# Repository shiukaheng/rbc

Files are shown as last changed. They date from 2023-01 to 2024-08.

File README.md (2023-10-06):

# 🤖 RoboCapture
A photogrammetry robot designed from scratch to autonomously scan indoor spaces.

## 🛠 Development

- **Cross-Platform**: This repository is designed to be cross-platform, working on Windows, MacOS, and Linux. We leverage Docker and the devcontainer extension in VSCode to achieve this.
  
- **Testing**: Most of the development and testing have been done on Linux. However, it might require slight adjustments when setting up on other operating systems.

### 🔧 Pre-requisites

1. `$(hostname).local` should be broadcasted on the network using mDNS. This applies to both the robot and the development computer.
2. Docker must be running on a Linux environment.

### 🍎 MacOS Specifics

If you're on a Mac, you might need to adjust the Docker permissions:
```bash
sudo chown -R $(whoami) ~/.docker
```
This ensures Docker can run without requiring sudo every time.

### 🖥️ X11 Authentication

For enabling X11 forwarding, execute the following command on the host computer:
```bash
xhost +local:docker
```

### 📝 Notes
Please double-check the file permissions before making a commit to ensure they are appropriate, due to docker created files being owned by `root`. Fix shall be issued soon.

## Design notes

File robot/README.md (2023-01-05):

# 🦚 Robocock

Project Robocock is a versatile fully automated high-resolution interior photogrammetry solution.

The system will utilise [SLAM](https://www.notion.so/About-caf9711042f84a92b1a0a05f0bd871f7), an [omni wheel system](https://en.wikipedia.org/wiki/Omni_wheel), and a custom path planning algorithm to provide a moving platform to mount cameras on, of which will be connected to the onboard computer to automatically acquire images for [photogrammetry](https://www.notion.so/About-caf9711042f84a92b1a0a05f0bd871f7) while traversing the interior space.

For the field of 3D capture, this tool will be a valuable replacement to [mainstream ground-based LIDAR scanning](https://en.wikipedia.org/wiki/Lidar#Surveying), which captures geometry well, but not so much on model texture detail important for model visualization; or drone photogrammetry, since it may be impractical to fly drones in interior spaces. 

Moreover, in the recent rise in [neural radiance field research](https://www.matthewtancik.com/nerf), the dense image datasets our automation captures may also be increasingly useful.

## Roadmap
- [x]  Assemble frame
- [ ]  Install motors and wheels
- [ ]  Assemble electronics to drive wheels
- [ ]  Add sensors to frame
- [ ]  Path planning
- [ ]  Photogrammetry integration

## Setting ups

1) create directory: ~/dev_ws/src
2) clone this repository under the directory as mentioned
3) cd to dev_ws
4) build by entering: colcon build --symlink-install

## Other useful commands

1) setup bash with: source install/setup.bash
2) launch ROS with: ros2 launch robocock rsp.launch.py
3) run rviz with: ros2 run rviz2 rviz2
4) run empty joint state publisher with: ros2 run joint_state_publisher_gui joint_state_publisher_gui
5) to run gazebo with robot, launch with: ros2 launch robocock launch_sim.launch.py

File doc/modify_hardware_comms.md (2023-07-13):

- Change the motor_state.h under controller code if necessary.
- Change rbc messages
- Change hardware_parameter_server
- Change RobotHW (If impacted setpoint)

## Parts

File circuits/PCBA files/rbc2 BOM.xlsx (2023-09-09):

Comment | Designator | Footprint | JLCPCB Part #
1uF | C1 | Capacitor_SMD:C_0603_1608Metric | C696843
270uF | C2, C11, C12, C24 | EEHZS1H221P | C79124
4.7uF | C3 | Capacitor_SMD:C_1206_3216Metric | C412300
10nF | C4 | Capacitor_SMD:C_0402_1005Metric | C482489
100nF | C5, C6, C13, C14, C19, C20, C21, C22, C23, C25, C30, C31, C33 | Capacitor_SMD:C_0402_1005Metric | C2649519
10pF | C7 | Capacitor_SMD:C_0603_1608Metric | C2171298
10nF | C8, C15, C16, C26 | Capacitor_SMD:C_0805_2012Metric | C27071
22uF | C9 | Capacitor_SMD:C_1206_3216Metric | C304004
100uF | C10, C17, C18, C27 | 16SVF180M | C136275
220nF | C28, C29, C32 | Capacitor_SMD:C_0805_2012Metric | C913663
450mV 3A Schottky Diode | D1, D2, D3, D5 | Diode_SMD:D_SMA | C17101
Yellow LED | D4 | Diode_SMD:D_0805_2012Metric | C84261
Green LED | D6, D7, D8, D9 | Diode_SMD:D_0805_2012Metric | C63855
Red LED | D10 | Diode_SMD:D_0805_2012Metric | C86865
LT8609AEDDM#PBF | IC1 | SON50P300X300X80-11N-D | C673976
LM2678SX-ADJ/NOPB | IC2, IC3, IC4, IC5 | KTW0007B | C40844
BTN70301EPAXUMA1 | IC6, IC7, IC8, IC9, IC10, IC11 | Infineon_PG-TSDSO-14-22 | C3655686
DNP | J1 | TerminalBlock_Phoenix:TerminalBlock_Phoenix_MKDS-3-2-5.08_1x02_P5.08mm_Horizontal
DNP | J2 | Connector_PinHeader_2.54mm:PinHeader_2x02_P2.54mm_Vertical
DNP | J3 | Connector_PinHeader_2.54mm:PinHeader_2x02_P2.54mm_Vertical
DNP | J4 | Connector_PinHeader_2.54mm:PinHeader_2x02_P2.54mm_Vertical
DNP | J5 | TerminalBlock_Phoenix:TerminalBlock_Phoenix_MKDS-3-2-5.08_1x02_P5.08mm_Horizontal
DNP | J6 | Connector_Molex:Molex_Micro-Fit_3.0_43045-0612_2x03_P3.00mm_Vertical
DNP | J7, J8 | Connector_Molex:Molex_Micro-Fit_3.0_43045-0412_2x02_P3.00mm_Vertical
DNP | J9, J10, J11 | Connector_Molex:Molex_Micro-Fit_3.0_43045-0612_2x03_P3.00mm_Vertical
2.2uH | L1 | INDC4441X200N | C719179
22uH | L2, L3, L4, L6 | INDPM110100X400N | C2047201
10uH | L5 | Inductor_SMD:L_0805_2012Metric | C88172
18.2k | R1 | Resistor_SMD:R_0603_1608Metric_Pad0.98x0.95mm_HandSolder | C844532
1k | R2, R7, R8, R18 | Resistor_SMD:R_0201_0603Metric | C138165
187k | R3 | Resistor_SMD:R_0603_1608Metric | C227629
8.87k | R4, R9, R10, R20 | Resistor_SMD:R_0603_1608Metric | C862310
1M | R5, R12 | Resistor_SMD:R_0402_1005Metric | C144787
100k | R6 | Resistor_SMD:R_0201_0603Metric | C100127
10k | R11, R19 | Resistor_SMD:R_0402_1005Metric | C144807
1.6k | R13 | Resistor_SMD:R_0805_2012Metric_Pad1.20x1.40mm_HandSolder | C316776
3.3k | R14 | Resistor_SMD:R_1206_3216Metric_Pad1.30x1.75mm_HandSolder | C104771
300 | R15, R21, R22, R23, R24, R25 | Resistor_SMD:R_0603_1608Metric_Pad0.98x0.95mm_HandSolder | C203500
82k ±1% | R16 | Resistor_SMD:R_0603_1608Metric_Pad0.98x0.95mm_HandSolder | C103831
18k ±5% | R17 | Resistor_SMD:R_0603_1608Metric_Pad0.98x0.95mm_HandSolder | C445839
4.7k | R26, R27, R28, R29, R32, R33, R34, R35, R36, R37, R38, R39, R40, R41, R42, R43, R44, R45, R47, R48, R49, R50, R51, R52 | Resistor_SMD:R_1206_3216Metric | C432834
1.2k | R30, R31, R46 | Resistor_SMD:R_1206_3216Metric | C340507
RESET Switch | S1 | FSM4JSMATR | C86487
CSTCE16M0V53-R0 | U1 | CSTCE16M0V53R0 | C32180
ATmega2560-16A | U2 | Package_QFP:TQFP-100_14x14mm_P0.5mm | C22460

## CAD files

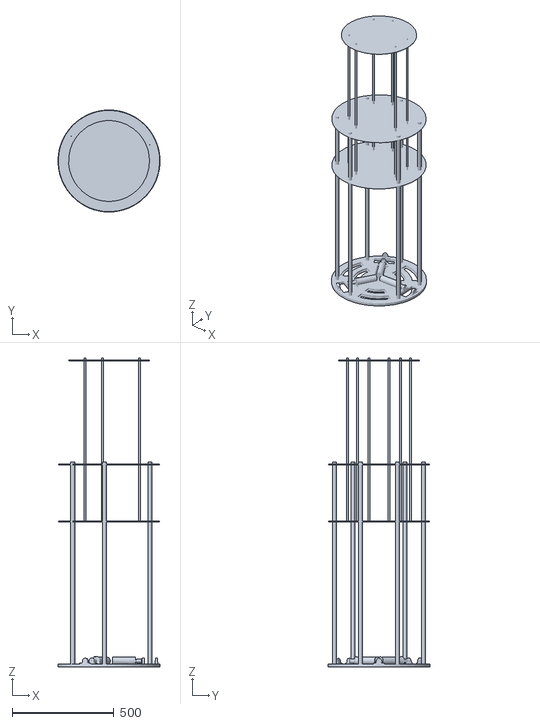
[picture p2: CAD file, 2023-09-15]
ros/rbc_base/meshes/frame_ultra_low_poly.stl
500.2 x 500.0 x 1515.0

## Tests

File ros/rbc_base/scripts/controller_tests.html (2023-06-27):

# Closed-loop testing¶

In [ ]:

%matplotlib inline
from robodev import *

In [ ]:

d = Robodev()
d.set_global_velocity(0)

[INFO] [1687739845.622243]: Waiting for base_state to start publishing...
[INFO] [1687739845.644485]: Got first message from base_state, ready!

In [ ]:

# Prerequisites
track = d.create_track().add_saw_wave(max_vel=5.0, duration=15.0, periods=3)

def apply_settings(mode: int, p_in: float, i_in: float, d_in: float, bias: float, initial_i: float = 0, plot_exclude_wheels: list = [2]):
    d.set_global_velocity(0)
    d.set_global_adaptive_state(initial_i)
    d.set_global_control_params(p_in, i_in, d_in, bias, mode)
    result = track.run()
    d.set_global_velocity(0)
    d.set_global_adaptive_state(0)
    result.plot(plot_exclude_wheels)
    result.plot_setpoint_v_velocity(plot_exclude_wheels)
    result.plot_all(plot_exclude_wheels)
    return result

# Simple PI controller¶

In [ ]:

pi = apply_settings(
    mode=1,
    p_in=40,
    i_in=10,
    d_in=0,
    bias=0
)

# PI controller with flipping biases and integrals¶

In [ ]:

pif = apply_settings(
    mode=2,
    p_in=40,
    i_in=10,
    d_in=0,
    bias=50
)

# Adaptive PID controller¶

In [ ]:

pid = apply_settings(
    mode=3,
    p_in=40,
    i_in=15.,
    d_in=0,
    bias=50
)

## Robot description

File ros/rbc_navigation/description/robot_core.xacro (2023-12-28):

<?xml version="1.0"?>
<robot xmlns:xacro="http://www.ros.org/wiki/xacro">

    <xacro:include filename="inertial_macros.xacro"/>

    <!-- links and joints go here -->

    <!-- The rest of the robot can be described from base_link, which is the centre point of the four driving wheels -->
    <link name="base_link">
    </link>

    <!-- chassis joint goes here. It connects chassis to base_link via fixed joint -->
    <joint name="chassis_joint" type="fixed">
        <parent link="base_link"/>
        <child link="chassis"/>
        <origin xyz="0 0 0"/>
    </joint> launch-prefix="bash -c 'sleep 5; $0 $@'"
    <!-- chassis description goes here. It describes the chassis of the bot which is a 54cm x 54cm x 150cm box -->
    <link name="chassis">
        <visual>
            <!-- by default, the origin is centred around the link origin, so offset it by half the height -->
            <!-- <origin xyz="0 0 0.75" rpy="0 0 0"/> -->
            <geometry>
                <!-- <box size="0.54 0.54 1.5"/> -->
                <mesh filename="package://rbc_base/meshes/frame_ultra_low_poly.stl" scale="0.001 0.001 0.001"/>
                <!-- <mesh filename="model://frame_ultra_low_poly.stl"/> -->
            </geometry>
            <material name="white"/>
        </visual>
        <!-- physics model -->
        <collision>
            <origin xyz="0 0 0.77" rpy="0 0 0"/>
            <geometry>
                <cylinder length="1.54" radius="0.25"/>
            </geometry>
        </collision>
        <xacro:inertial_cylinder mass="20" length="1.54" radius="0.25">
            <origin xyz="0 0 0.77" rpy="0 0 0"/>
        </xacro:inertial_cylinder>
    </link>
    <joint name="laser_joint" type="fixed">
        <parent link="chassis"/>
        <child link="laser"/>
        <origin xyz="0 0 0.07" rpy="0 0 0"/>
    </joint>
    <link name="laser">
        <visual>
            <origin xyz="0 0 0" rpy="0 0 0"/>
            <geometry>
                <cylinder length="0.05" radius="0.05"/>
            </geometry>
            <material name="black"/>
        </visual>
    </link>
    <!-- gazebo specific description -->
    <gazebo reference="chassis">
        <material>Gazebo/White</material>
    </gazebo>

    <!-- WHEEL 1 (CLOCKWISE) -->
    <joint name="wheel_1_joint" type="continuous">
        <parent link="base_link"/>
        <child link="wheel_1"/>
        <origin xyz="0.2 0 0" rpy="0 -${pi/2} 0"/>
        <axis xyz="0 0 1"/>
    </joint>

    <link name="wheel_1">
        <visual>
            <geometry>      
                <cylinder length="0.038" radius="0.05" />
            </geometry>
            <material name="black"/>
        </visual>
        <collision>
            <geometry>      
                <cylinder length="0.038" radius="0.05" />
            </geometry>
        </collision>
        <xacro:inertial_cylinder mass="0.2" length="0.038" radius="0.05">
            <origin xyz="0 0 0" rpy="0 0 0"/>
        </xacro:inertial_cylinder>
    </link>

    <gazebo reference="wheel_1">
        <material>Gazebo/Black</material>
        <mu1 value="0.2"/>
        <mu2 value="1.5"/>
        <kp value="10000000.0" />
        <kd value="10000.0" />
        <fdir1 value="0 0 1"/>
        <maxContacts value= "1"/>
    </gazebo>

    <!-- WHEEL 2 -->
    <joint name="wheel_2_joint" type="continuous">
        <parent link="base_link"/>
        <child link="wheel_2"/>
        <origin xyz="-0.1 -0.1732050808 0" rpy="0 ${pi/2} ${pi/3}"/>
        <axis xyz="0 0 1"/>
    </joint>

    <link name="wheel_2">
        <visual>
            <geometry>      
                <cylinder length="0.038" radius="0.05" />
            </geometry>
            <material name="black"/>
        </visual>
        <collision>
            <geometry>      
                <cylinder length="0.038" radius="0.05" />
            </geometry>
        </collision>
        <xacro:inertial_cylinder mass="0.2" length="0.038" radius="0.05">
            <origin xyz="0 0 0" rpy="0 0 0"/>
        </xacro:inertial_cylinder>
    </link>

    <gazebo reference="wheel_2">
        <material>Gazebo/Black</material>
        <mu1 value="0.2"/>
        <mu2 value="1.5"/>
        <kp value="10000000.0" />
        <kd value="10000.0" />
        <fdir1 value="0 0 1"/>
        <maxContacts value= "1"/>
    </gazebo>

    <!-- WHEEL 3 -->
    <joint name="wheel_3_joint" type="continuous">
        <parent link="base_link"/>
        <child link="wheel_3"/>
        <origin xyz="-0.1 0.1732050808 0" rpy="0 ${pi/2} -${pi/3}"/>
        <axis xyz="0 0 1"/>
    </joint>

    <link name="wheel_3">
        <visual>
            <geometry>      
                <cylinder length="0.038" radius="0.05" />
            </geometry>
            <material name="black"/>
        </visual>
        <collision>
            <geometry>      
                <cylinder length="0.038" radius="0.05" />
            </geometry>
        </collision>
        <xacro:inertial_cylinder mass="0.2" length="0.038" radius="0.05">
            <origin xyz="0 0 0" rpy="0 0 0"/>
        </xacro:inertial_cylinder>
    </link>

    <gazebo reference="wheel_3">
        <material>Gazebo/Black</material>
        <mu1 value="0.2"/>
        <mu2 value="1.5"/>
        <kp value="10000000.0" />
        <kd value="10000.0" />
        <fdir1 value="0 0 1"/>
        <maxContacts value= "1"/>
    </gazebo>

    <!-- Transmissions -->
    <transmission name="tran1">
        <type>transmission_interface/SimpleTransmission</type>
        <joint name="wheel_1_joint">
            <hardwareInterface>hardware_interface/VelocityJointInterface</hardwareInterface>
        </joint>
        <actuator name="motor_1">
            <hardwareInterface>VelocityJointInterface</hardwareInterface>
            <mechanicalReduction>1</mechanicalReduction>
        </actuator>
    </transmission>

    <transmission name="tran2">
        <type>transmission_interface/SimpleTransmission</type>
        <joint name="wheel_2_joint">
            <hardwareInterface>hardware_interface/VelocityJointInterface</hardwareInterface>
        </joint>
        <actuator name="motor_2">
            <hardwareInterface>VelocityJointInterface</hardwareInterface>
            <mechanicalReduction>1</mechanicalReduction>
        </actuator>
    </transmission>

    <transmission name="tran3">
        <type>transmission_interface/SimpleTransmission</type>
        <joint name="wheel_3_joint">
            <hardwareInterface>hardware_interface/VelocityJointInterface</hardwareInterface>
        </joint>
        <actuator name="motor_3">
            <hardwareInterface>VelocityJointInterface</hardwareInterface>
            <mechanicalReduction>1</mechanicalReduction>
        </actuator>
    </transmission>

    <gazebo>
        <plugin name="gazebo_ros_control" filename="libgazebo_ros_control.so">
        </plugin>
    </gazebo>

</robot>

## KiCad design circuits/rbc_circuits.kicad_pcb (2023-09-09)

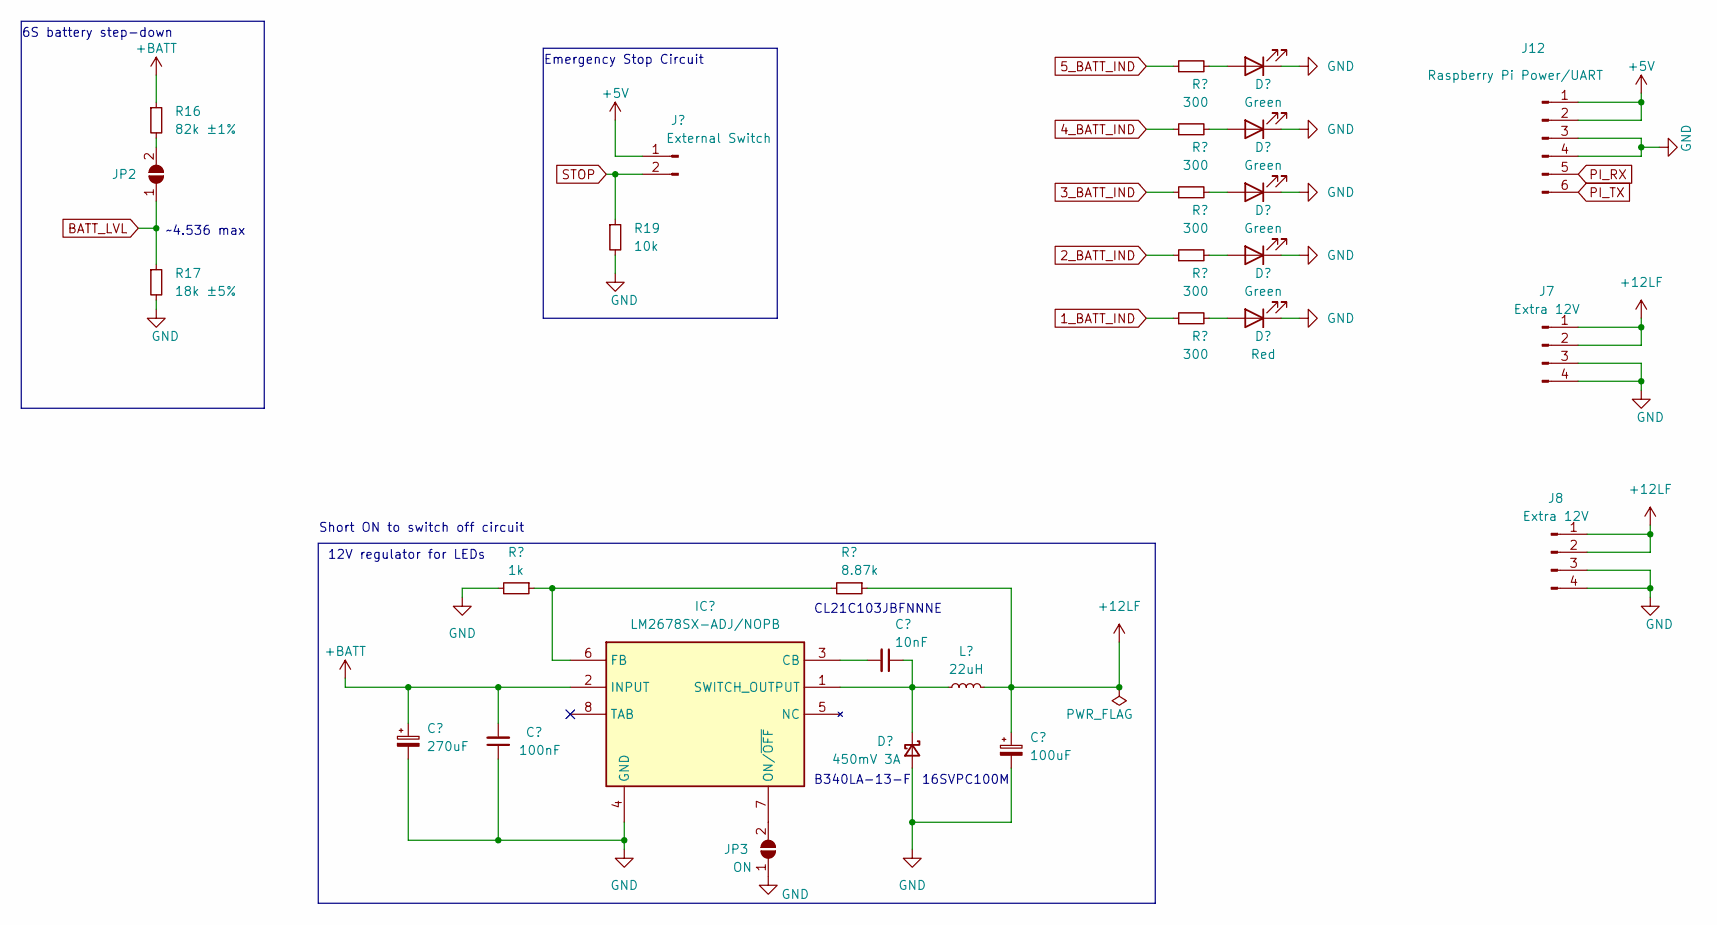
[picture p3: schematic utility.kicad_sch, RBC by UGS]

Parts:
C24: 270uF; EEHZS1H221P
C25: 100nF; C_0402_1005Metric
C26: 10nF; C_0805_2012Metric
C27: 100uF; 16SVF180M
D5: 450mV 3A; D_SMA
D6: Green; D_0805_2012Metric; Part No. 17-21/GHC-XS1T2M/3T
D7, D8, D9: Green; D_0805_2012Metric
D10: Red; D_0805_2012Metric; Part No. 17-215/R6C-AQ1R2B/3T
IC5: LM2678SX-ADJ/NOPB; KTW0007B_custom; Mouser Part Number 926-LM2678SX50NOPB
J5: External Switch; TerminalBlock_Phoenix_MKDS-3-2-5.08_1x02_P5.08mm_Horizontal
J7, J8: Extra 12V; Molex_Micro-Fit_3.0_43045-0412_2x02_P3.00mm_Vertical
J12: Raspberry Pi Power/UART; Molex_Micro-Fit_3.0_43045-0612_2x03_P3.00mm_Vertical
JP2: SolderJumper_2_Open; SolderJumper-2_P1.3mm_Open_RoundedPad1.0x1.5mm
JP3: ON; SolderJumper-2_P1.3mm_Open_RoundedPad1.0x1.5mm
L6: 22uH; INDPM110100X400N
R16: 82k ±1%; R_0603_1608Metric_Pad0.98x0.95mm_HandSolder; Part No. RTT038202FTP
R17: 18k ±5%; R_0603_1608Metric_Pad0.98x0.95mm_HandSolder
R18: 1k; R_0201_0603Metric
R19: 10k; R_0402_1005Metric
R20: 8.87k; R_0603_1608Metric
R21, R22, R23, R24, R25: 300; R_0603_1608Metric_Pad0.98x0.95mm_HandSolder

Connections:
1_BATT_IND: R25.1; also elsewhere on the board
2_BATT_IND: R24.1; also elsewhere on the board
3_BATT_IND: R23.1; also elsewhere on the board
4_BATT_IND: R22.1; also elsewhere on the board
5_BATT_IND: R21.1; also elsewhere on the board
+5V: J5.1; also elsewhere on the board
+12LF: C27.1, J7.1, J7.2, J8.1, J8.2, L6.2, R20.1
+BATT: C24.1, C25.2, IC5.2 (INPUT), R16.1; also elsewhere on the board
BATT_LVL: JP2.1 (A), R17.1; also elsewhere on the board
GND: C24.2, C25.1, C27.2, D5.2 (A), D6.1 (K), D7.1 (K), D8.1 (K), D9.1 (K), D10.1 (K), IC5.4 (GND), J7.3, J7.4, J8.3, J8.4, JP3.1 (A), R17.2, R18.2, R19.2; also elsewhere on the board
unnamed: C26.1, D5.1 (K), IC5.1 (SWITCH_OUTPUT), L6.1
unnamed: D6.2 (A), R21.2
unnamed: D7.2 (A), R22.2
unnamed: D8.2 (A), R23.2
unnamed: D9.2 (A), R24.2
unnamed: D10.2 (A), R25.2
unnamed: C26.2, IC5.3 (CB)
unnamed: IC5.6 (FB), R18.1, R20.2
unnamed: IC5.7 (ON/~OFF), JP3.2 (B)
unnamed: JP2.2 (B), R16.2
STOP: J5.2, R19.1; also elsewhere on the board

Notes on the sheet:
~4.536 max
6S battery step-down
16SVPC100M
12V regulator for LEDs
Short ON to switch off circuit
Emergency Stop Circuit
CL21C103JBFNNNE
B340LA-13-F

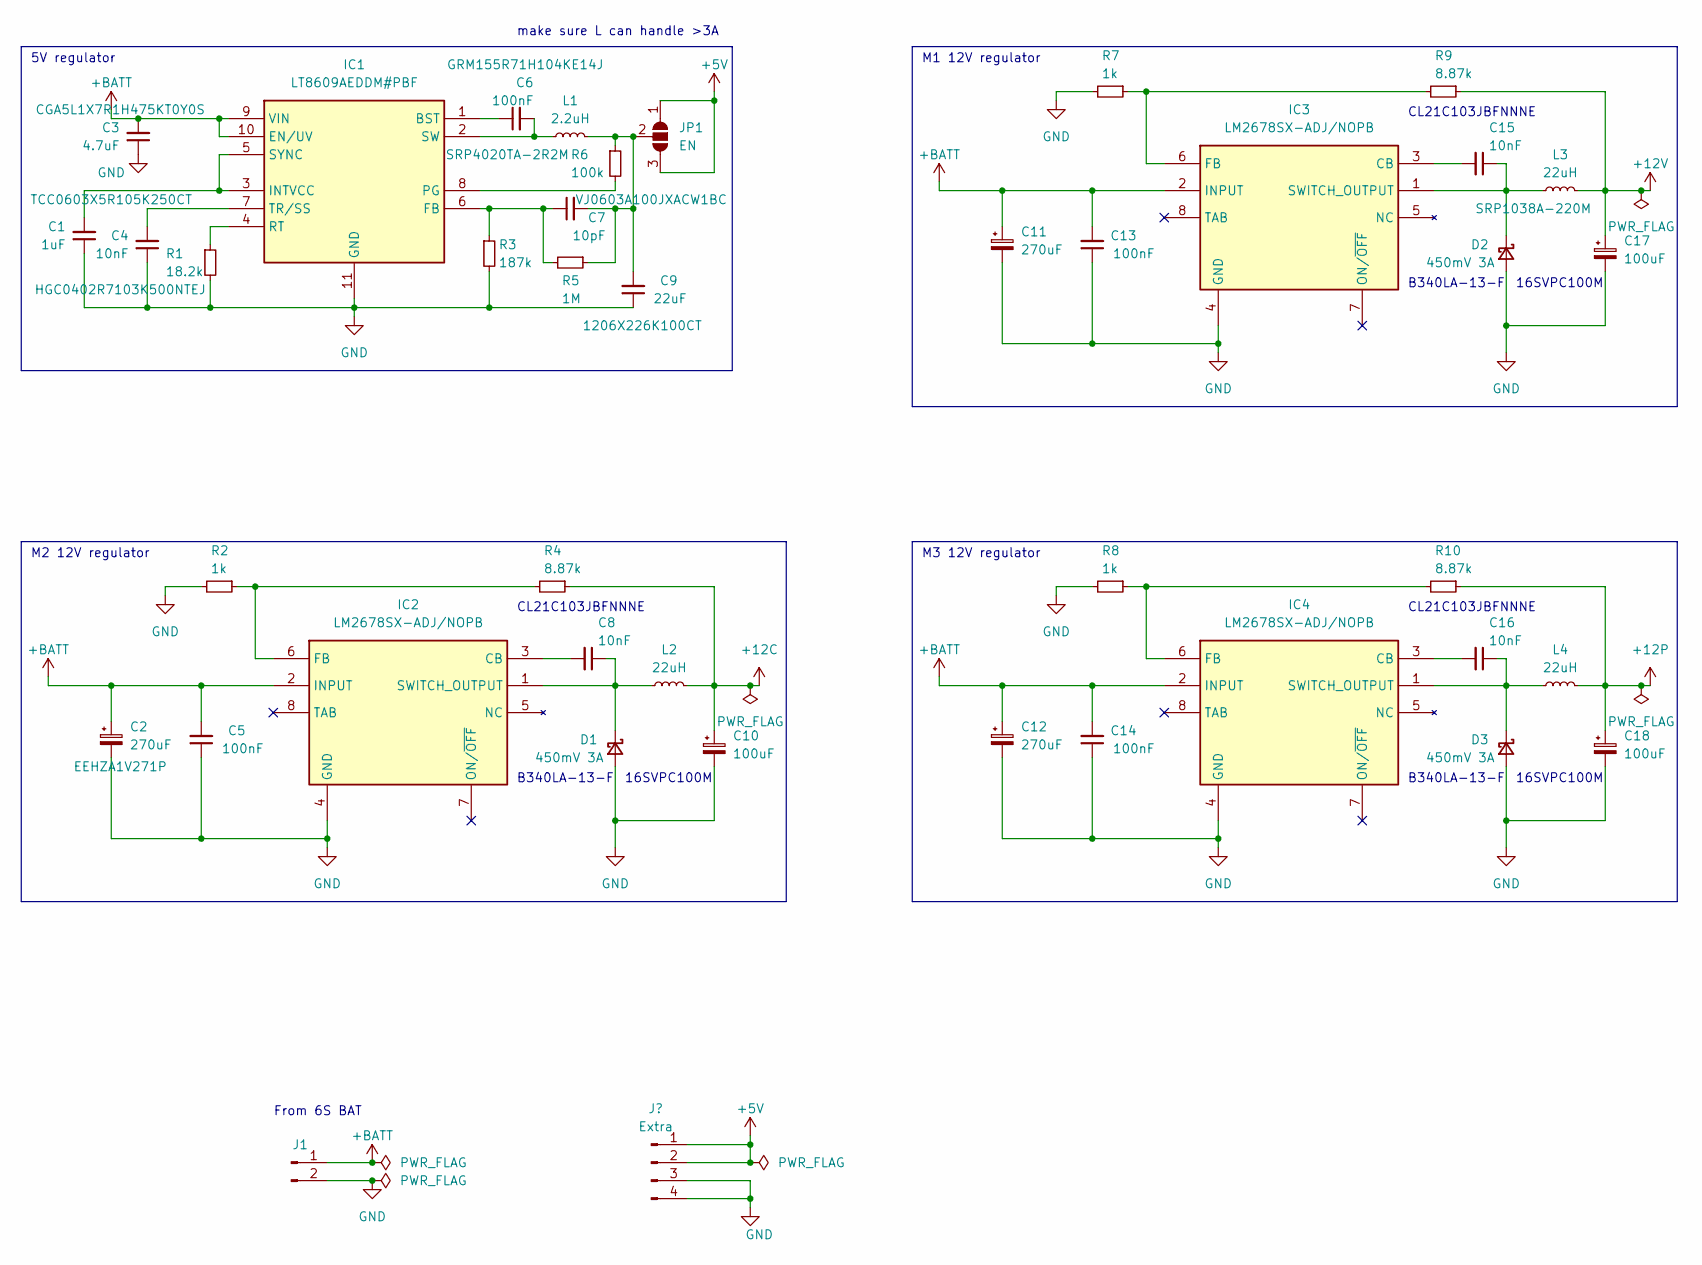
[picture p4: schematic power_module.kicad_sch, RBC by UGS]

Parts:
C1: 1uF; C_0603_1608Metric; Part No. TCC0603X5R105K250CT
C2: 270uF; EEHZS1H221P; Part No. EEHZA1V271P
C3: 4.7uF; C_1206_3216Metric; Part No. CGA5L1X7R1H475KT0Y0S
C4: 10nF; C_0402_1005Metric; Part No. HGC0402R7103K500NTEJ
C5, C13, C14: 100nF; C_0402_1005Metric
C6: 100nF; C_0402_1005Metric; Part No. GRM155R71H104KE14J
C7: 10pF; C_0603_1608Metric; Part No. VJ0603A100JXACW1BC
C8, C15, C16: 10nF; C_0805_2012Metric
C9: 22uF; C_1206_3216Metric; Part No. 1206X226K100CT
C10, C17, C18: 100uF; 16SVF180M
C11, C12: 270uF; EEHZS1H221P
D1, D2, D3: 450mV 3A; D_SMA
IC1: LT8609AEDDM#PBF; SON50P300X300X80-11N-D; Mouser Part Number 584-LT8609AEDDM#PBF
IC2, IC3, IC4: LM2678SX-ADJ/NOPB; KTW0007B_custom; Mouser Part Number 926-LM2678SX50NOPB
J1: Conn_01x02_Pin; TerminalBlock_Phoenix_MKDS-3-2-5.08_1x02_P5.08mm_Horizontal
J2: Extra; PinHeader_2x02_P2.54mm_Vertical
JP1: EN; SolderJumper-3_P2.0mm_Open_TrianglePad1.0x1.5mm
L1: 2.2uH; INDC4441X200N; Part No. SRP4020TA-2R2M
L2, L4: 22uH; INDPM110100X400N
L3: 22uH; INDPM110100X400N; Part No. SRP1038A-220M
R1: 18.2k; R_0603_1608Metric_Pad0.98x0.95mm_HandSolder; Part No. CRCW060318K2FKEA
R2: 1k; R_0201_0603Metric; Part No. RC0201FR-071KL
R3: 187k; R_0603_1608Metric; Part No. AC0603FR-07187KL
R4: 8.87k; R_0603_1608Metric; Part No. RT0603BRE078K87L
R5: 1M; R_0402_1005Metric; Part No. AC0402FR-071ML
R6: 100k; R_0201_0603Metric
R7, R8: 1k; R_0201_0603Metric
R9, R10: 8.87k; R_0603_1608Metric

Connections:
+5V: J2.1, J2.2, JP1.1 (A), JP1.3 (B); also elsewhere on the board
+12C: C10.1, L2.2, R4.1; also elsewhere on the board
+12P: C18.1, L4.2, R10.1; also elsewhere on the board
+12V: C17.1, L3.2, R9.1; also elsewhere on the board
+BATT: C2.1, C3.2, C5.2, C11.1, C12.1, C13.2, C14.2, IC1.9 (VIN), IC1.10 (EN/UV), IC2.2 (INPUT), IC3.2 (INPUT), IC4.2 (INPUT), J1.1; also elsewhere on the board
GND: C1.1, C2.2, C3.1, C4.1, C5.1, C9.1, C10.2, C11.2, C12.2, C13.1, C14.1, C17.2, C18.2, D1.2 (A), D2.2 (A), D3.2 (A), IC1.11 (GND), IC2.4 (GND), IC3.4 (GND), IC4.4 (GND), J1.2, J2.3, J2.4, R1.2, R2.2, R3.2, R7.2, R8.2; also elsewhere on the board
unnamed: C8.1, D1.1 (K), IC2.1 (SWITCH_OUTPUT), L2.1
unnamed: C15.1, D2.1 (K), IC3.1 (SWITCH_OUTPUT), L3.1
unnamed: C16.1, D3.1 (K), IC4.1 (SWITCH_OUTPUT), L4.1
unnamed: C6.1, IC1.1 (BST)
unnamed: C7.1, IC1.6 (FB), R3.1, R5.2
unnamed: C1.2, IC1.3 (INTVCC), IC1.5 (SYNC)
unnamed: IC1.8 (PG), R6.2
unnamed: IC1.4 (RT), R1.1
unnamed: C6.2, IC1.2 (SW), L1.1
unnamed: C4.2, IC1.7 (TR/SS)
unnamed: C8.2, IC2.3 (CB)
unnamed: IC2.6 (FB), R2.1, R4.2
unnamed: C15.2, IC3.3 (CB)
unnamed: IC3.6 (FB), R7.1, R9.2
unnamed: C16.2, IC4.3 (CB)
unnamed: IC4.6 (FB), R8.1, R10.2
unnamed: C7.2, C9.2, JP1.2 (C), L1.2, R5.1, R6.1

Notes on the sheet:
CL21C103JBFNNNE
16SVPC100M
B340LA-13-F
make sure L can handle >3A
From 6S BAT
M2 12V regulator
5V regulator
M3 12V regulator
M1 12V regulator

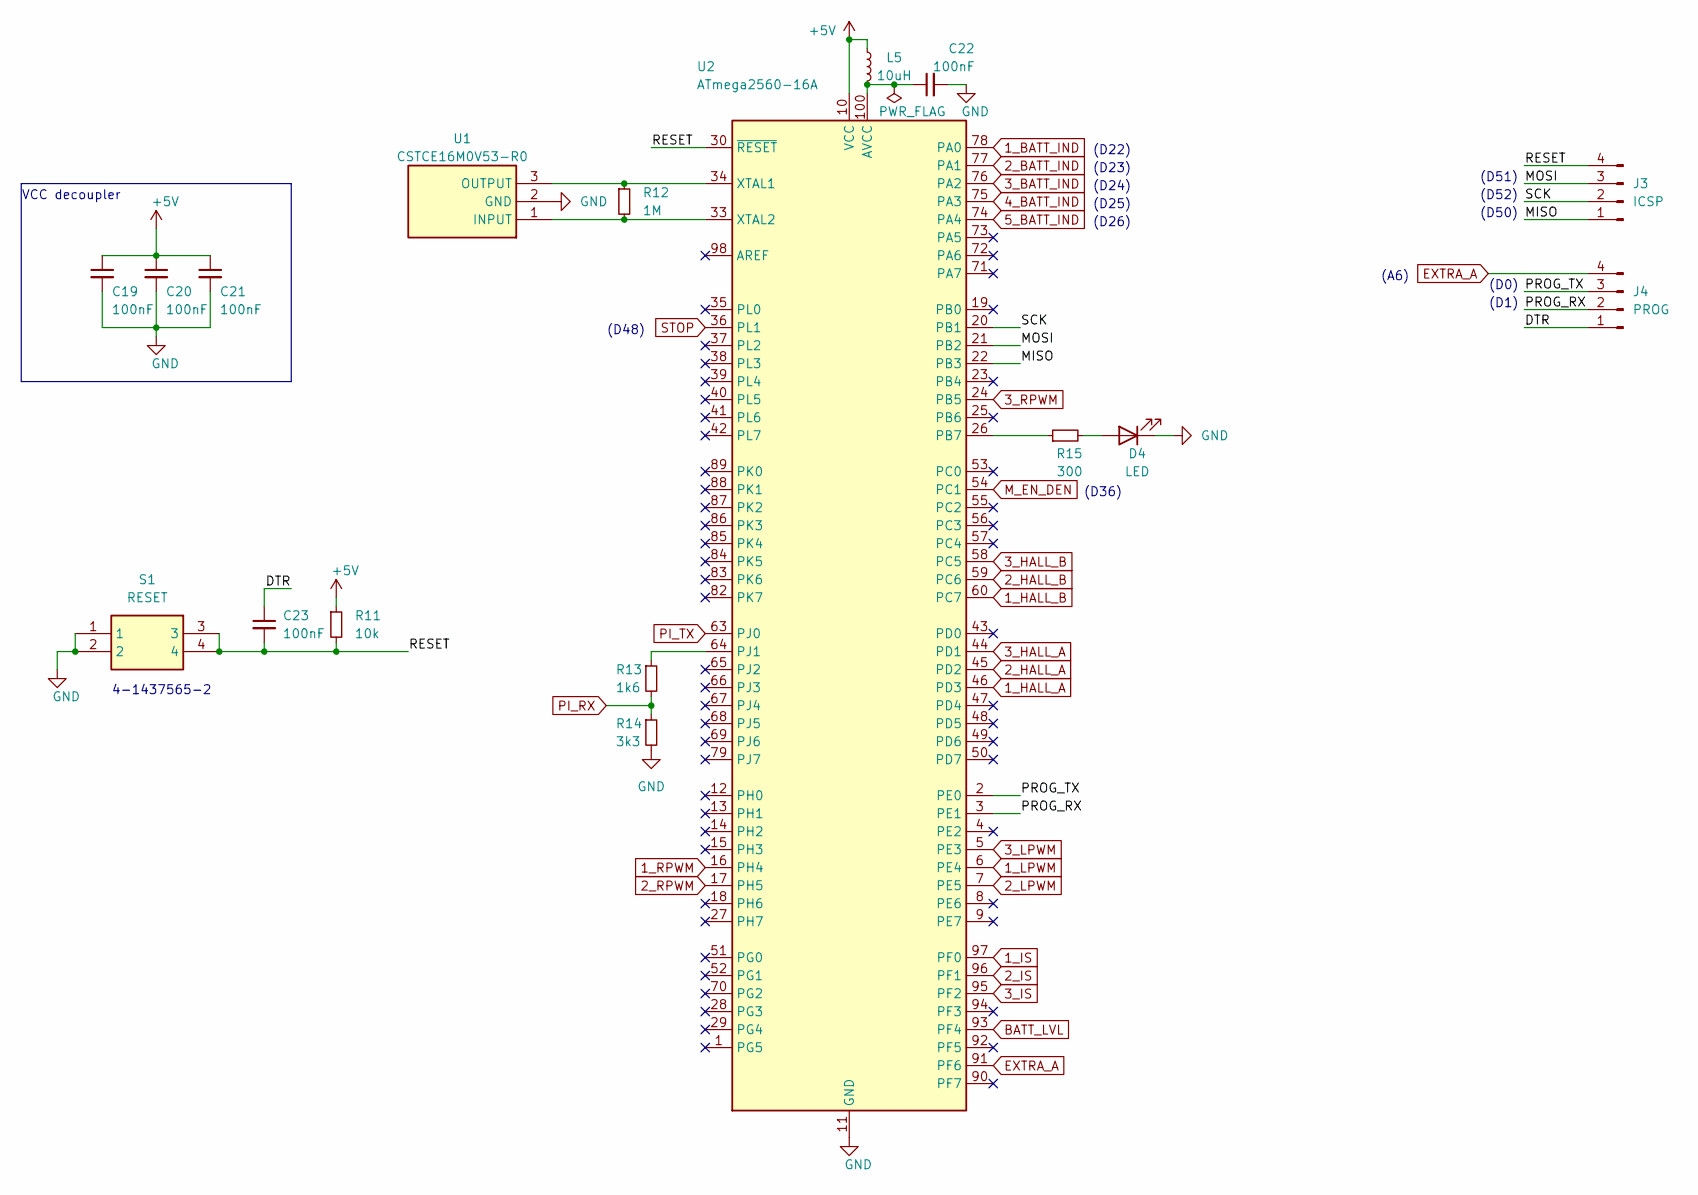
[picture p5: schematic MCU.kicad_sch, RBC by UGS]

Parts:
C19, C20, C21, C22, C23: 100nF; C_0402_1005Metric
D4: LED; D_0805_2012Metric; Part No. NCD0805Y1
J3: ICSP; PinHeader_2x02_P2.54mm_Vertical
J4: PROG; PinHeader_2x02_P2.54mm_Vertical
L5: 10uH; L_0805_2012Metric; Part No. MLZ2012M100HT000
R11: 10k; R_0402_1005Metric; Part No. AC0402FR-0710KL
R12: 1M; R_0402_1005Metric
R13: 1k6; R_0805_2012Metric_Pad1.20x1.40mm_HandSolder
R14: 3k3; R_1206_3216Metric_Pad1.30x1.75mm_HandSolder
R15: 300; R_0603_1608Metric_Pad0.98x0.95mm_HandSolder; Part No. CR0603-FX-3000ELF
S1: RESET; FSM4JSMATR; Mouser Part Number 506-FSM4JSMATR
U1: CSTCE16M0V53-R0; CSTCE16M0V53R0; Mouser Part Number 81-CSTNE16M0V530000R
U2: ATmega2560-16A; TQFP-100_14x14mm_P0.5mm

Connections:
1_BATT_IND: U2.78 (PA0); also elsewhere on the board
1_HALL_A: U2.46 (PD3); also elsewhere on the board
1_HALL_B: U2.60 (PC7); also elsewhere on the board
1_IS: U2.97 (PF0); also elsewhere on the board
1_LPWM: U2.6 (PE4); also elsewhere on the board
1_RPWM: U2.16 (PH4); also elsewhere on the board
2_BATT_IND: U2.77 (PA1); also elsewhere on the board
2_HALL_A: U2.45 (PD2); also elsewhere on the board
2_HALL_B: U2.59 (PC6); also elsewhere on the board
2_IS: U2.96 (PF1); also elsewhere on the board
2_LPWM: U2.7 (PE5); also elsewhere on the board
2_RPWM: U2.17 (PH5); also elsewhere on the board
3_BATT_IND: U2.76 (PA2); also elsewhere on the board
3_HALL_A: U2.44 (PD1); also elsewhere on the board
3_HALL_B: U2.58 (PC5); also elsewhere on the board
3_IS: U2.95 (PF2); also elsewhere on the board
3_LPWM: U2.5 (PE3); also elsewhere on the board
3_RPWM: U2.24 (PB5); also elsewhere on the board
4_BATT_IND: U2.75 (PA3); also elsewhere on the board
5_BATT_IND: U2.74 (PA4); also elsewhere on the board
+5V: C19.1, C20.1, C21.1, L5.1, R11.1, U2.10 (VCC), U2.31 (VCC), U2.61 (VCC), U2.80 (VCC); also elsewhere on the board
/MCU/DTR: C23.1, J4.1
/MCU/MISO: J3.1, U2.22 (PB3)
/MCU/MOSI: J3.3, U2.21 (PB2)
/MCU/PROG_RX: J4.2, U2.3 (PE1)
/MCU/PROG_TX: J4.3, U2.2 (PE0)
/MCU/RESET: C23.2, J3.4, R11.2, S1.3, S1.4, U2.30 (~RESET)
/MCU/SCK: J3.2, U2.20 (PB1)
BATT_LVL: U2.93 (PF4); also elsewhere on the board
EXTRA_A: J4.4, U2.91 (PF6)
GND: C19.2, C20.2, C21.2, C22.2, D4.1 (K), R14.2, S1.1, S1.2, U1.2 (GND), U2.11 (GND), U2.32 (GND), U2.62 (GND), U2.81 (GND), U2.99 (GND); also elsewhere on the board
M_EN_DEN: U2.54 (PC1); also elsewhere on the board
unnamed: D4.2 (A), R15.2
unnamed: R12.2, U1.1 (INPUT), U2.33 (XTAL2)
unnamed: R12.1, U1.3 (OUTPUT), U2.34 (XTAL1)
unnamed: C22.1, L5.2, U2.100 (AVCC)
unnamed: R15.1, U2.26 (PB7)
unnamed: R13.1, U2.64 (PJ1)
PI_RX: R13.2, R14.1; also elsewhere on the board
PI_TX: U2.63 (PJ0); also elsewhere on the board
STOP: U2.36 (PL1); also elsewhere on the board

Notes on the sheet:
(D52)
(D22)
(D23)
(D36)
(D25)
(D26)
(D51)
(D48)
VCC decoupler
(D0)
(D1)
(D50)
(A6)
4-1437565-2
(D24)

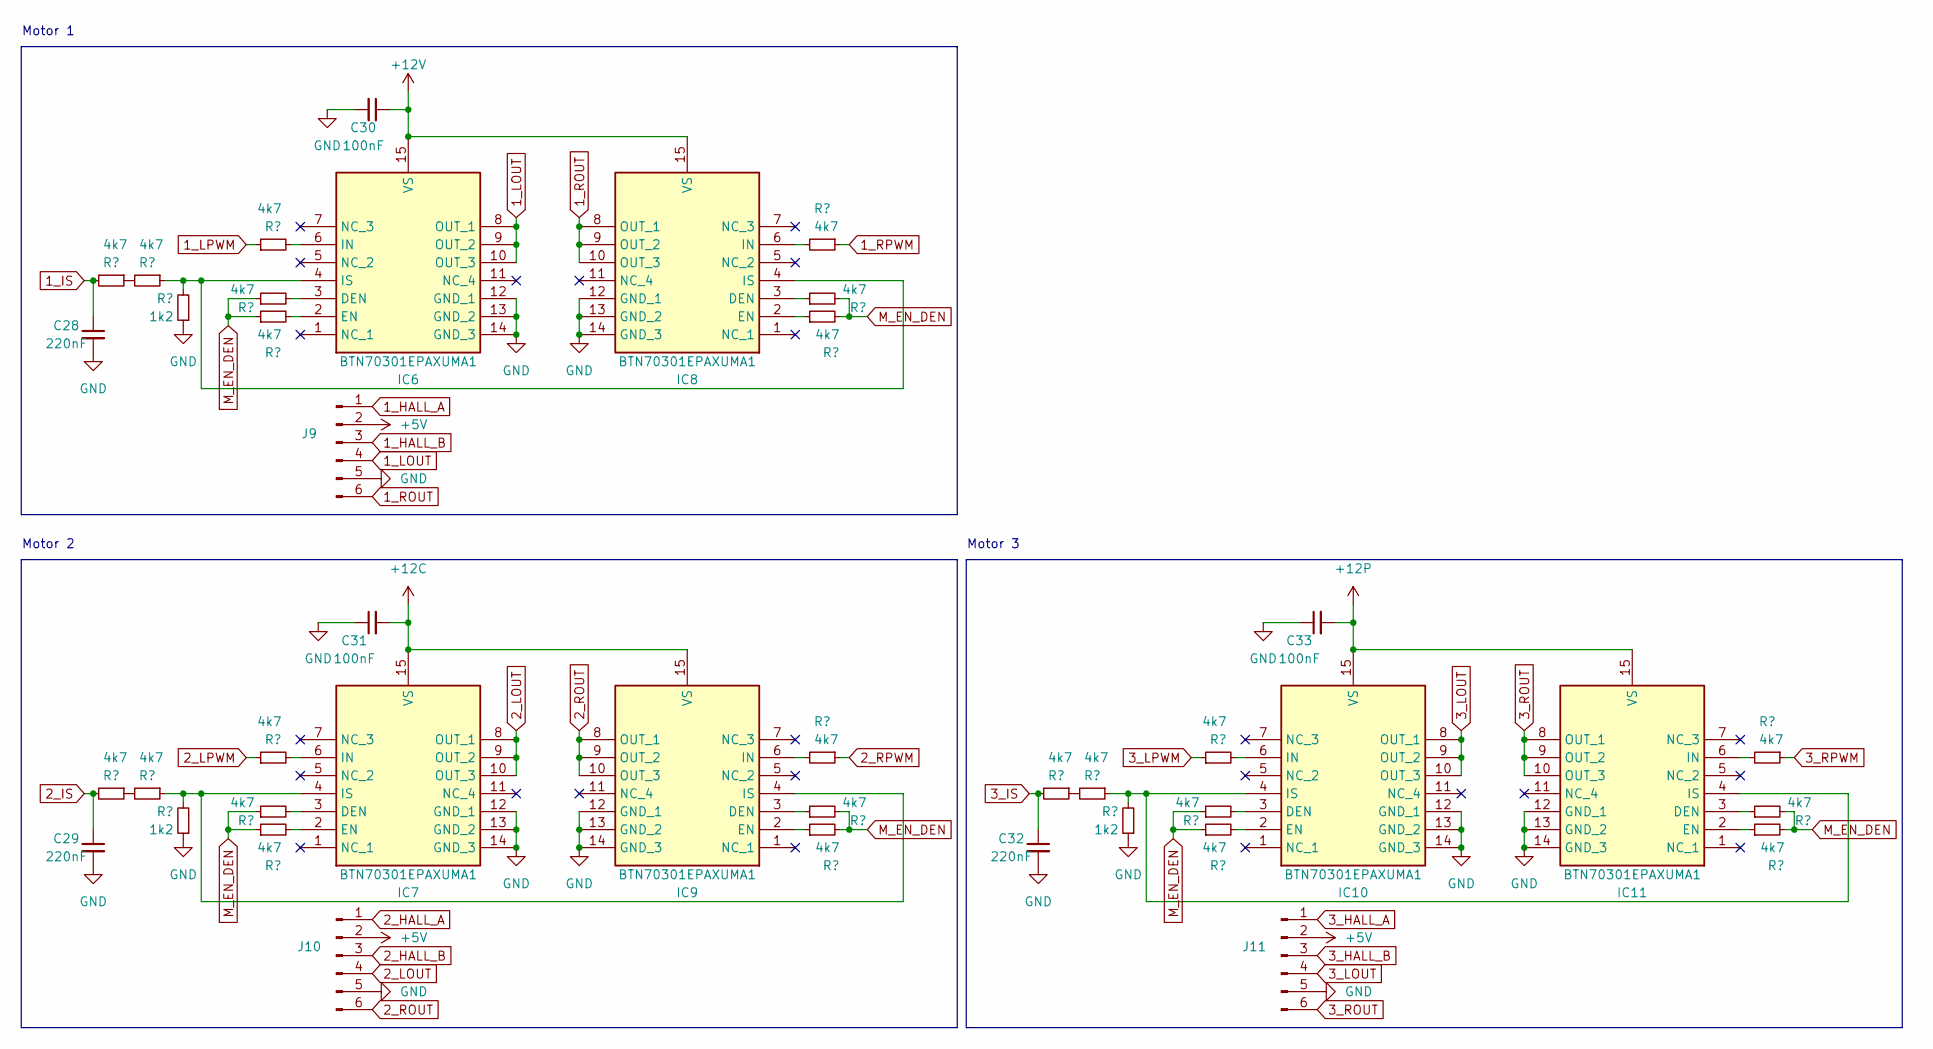
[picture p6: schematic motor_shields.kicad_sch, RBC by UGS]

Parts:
C28, C29, C32: 220nF; C_0805_2012Metric
C30, C31, C33: 100nF; C_0402_1005Metric
IC6, IC7, IC8, IC9, IC10, IC11: BTN70301EPAXUMA1; Infineon_PG-TSDSO-14-22_custom; Mouser Part Number 726-BTN70301EPAXUMA1
J9, J10, J11: Conn_01x06_Pin; Molex_Micro-Fit_3.0_43045-0612_2x03_P3.00mm_Vertical
R26, R27, R28, R29, R32, R33, R34, R35, R36, R37, R38, R39, R40, R41, R42, R43, R44, R45, R47, R48, R49, R50, R51, R52: 4k7; R_1206_3216Metric
R30, R31, R46: 1k2; R_1206_3216Metric

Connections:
1_HALL_A: J9.1; also elsewhere on the board
1_HALL_B: J9.3; also elsewhere on the board
1_IS: C28.1, R26.2; also elsewhere on the board
1_LOUT: IC6.8 (OUT_1), IC6.9 (OUT_2), IC6.10 (OUT_3), J9.4
1_LPWM: R32.1; also elsewhere on the board
1_ROUT: IC8.8 (OUT_1), IC8.9 (OUT_2), IC8.10 (OUT_3), J9.6
1_RPWM: R38.1; also elsewhere on the board
2_HALL_A: J10.1; also elsewhere on the board
2_HALL_B: J10.3; also elsewhere on the board
2_IS: C29.1, R27.2; also elsewhere on the board
2_LOUT: IC7.8 (OUT_1), IC7.9 (OUT_2), IC7.10 (OUT_3), J10.4
2_LPWM: R35.1; also elsewhere on the board
2_ROUT: IC9.8 (OUT_1), IC9.9 (OUT_2), IC9.10 (OUT_3), J10.6
2_RPWM: R41.1; also elsewhere on the board
3_HALL_A: J11.1; also elsewhere on the board
3_HALL_B: J11.3; also elsewhere on the board
3_IS: C32.1, R44.2; also elsewhere on the board
3_LOUT: IC10.8 (OUT_1), IC10.9 (OUT_2), IC10.10 (OUT_3), J11.4
3_LPWM: R47.1; also elsewhere on the board
3_ROUT: IC11.8 (OUT_1), IC11.9 (OUT_2), IC11.10 (OUT_3), J11.6
3_RPWM: R50.1; also elsewhere on the board
+5V: J9.2, J10.2, J11.2; also elsewhere on the board
+12C: C31.2, IC7.15 (VS), IC9.15 (VS); also elsewhere on the board
+12P: C33.2, IC10.15 (VS), IC11.15 (VS); also elsewhere on the board
+12V: C30.1, IC6.15 (VS), IC8.15 (VS); also elsewhere on the board
GND: C28.2, C29.2, C30.2, C31.1, C32.2, C33.1, IC6.12 (GND_1), IC6.13 (GND_2), IC6.14 (GND_3), IC7.12 (GND_1), IC7.13 (GND_2), IC7.14 (GND_3), IC8.12 (GND_1), IC8.13 (GND_2), IC8.14 (GND_3), IC9.12 (GND_1), IC9.13 (GND_2), IC9.14 (GND_3), IC10.12 (GND_1), IC10.13 (GND_2), IC10.14 (GND_3), IC11.12 (GND_1), IC11.13 (GND_2), IC11.14 (GND_3), J9.5, J10.5, J11.5, R30.1, R31.1, R46.1; also elsewhere on the board
M_EN_DEN: R33.1, R34.1, R36.1, R37.1, R39.2, R40.2, R42.2, R43.2, R48.1, R49.1, R51.2, R52.2; also elsewhere on the board
unnamed: IC6.3 (DEN), R33.2
unnamed: IC6.2 (EN), R34.2
unnamed: IC6.6 (IN), R32.2
unnamed: IC6.4 (IS), IC8.4 (IS), R28.1, R30.2
unnamed: IC7.3 (DEN), R36.2
unnamed: IC7.2 (EN), R37.2
unnamed: IC7.6 (IN), R35.2
unnamed: IC7.4 (IS), IC9.4 (IS), R29.1, R31.2
unnamed: IC8.3 (DEN), R39.1
unnamed: IC8.2 (EN), R40.1
unnamed: IC8.6 (IN), R38.2
unnamed: IC9.3 (DEN), R42.1
unnamed: IC9.2 (EN), R43.1
unnamed: IC9.6 (IN), R41.2
unnamed: IC10.3 (DEN), R48.2
unnamed: IC10.2 (EN), R49.2
unnamed: IC10.6 (IN), R47.2
unnamed: IC10.4 (IS), IC11.4 (IS), R45.1, R46.2
unnamed: IC11.3 (DEN), R51.1
unnamed: IC11.2 (EN), R52.1
unnamed: IC11.6 (IN), R50.2
unnamed: R26.1, R28.2
unnamed: R27.1, R29.2
unnamed: R44.1, R45.2

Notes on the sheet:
Motor 2
Motor 3
Motor 1

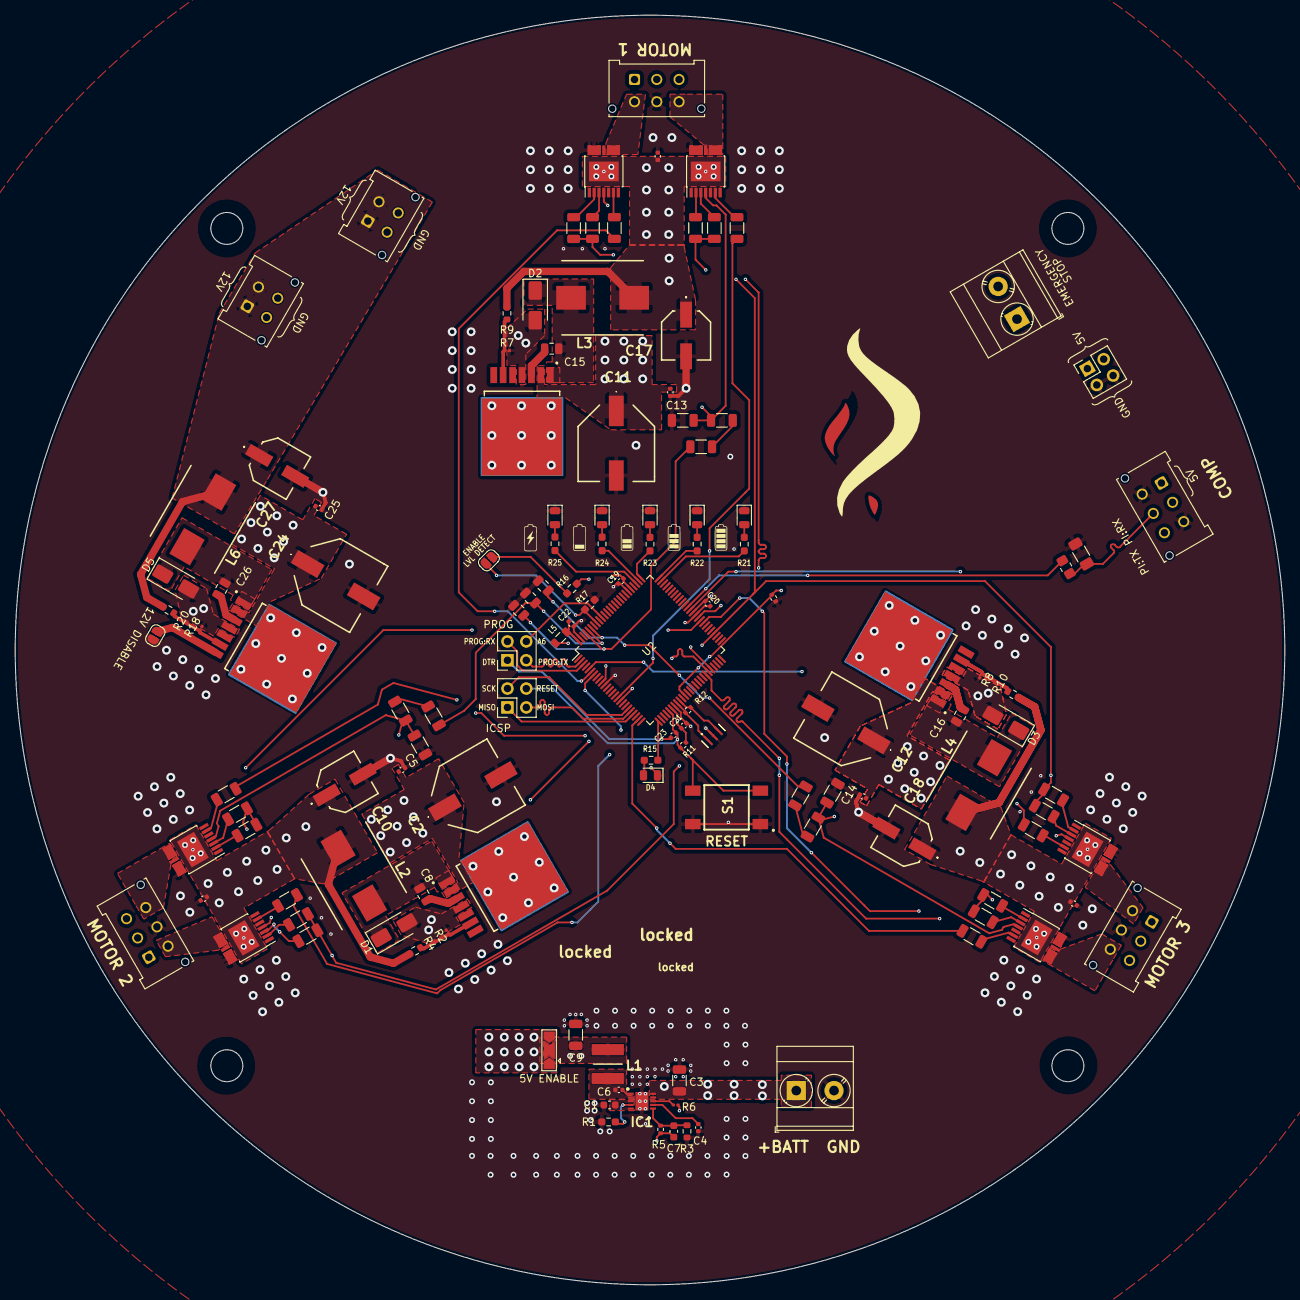
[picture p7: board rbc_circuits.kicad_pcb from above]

Board: 4 copper layers, 171.0 x 171.0 mm, 129 parts (0 on the bottom side), 103 nets.

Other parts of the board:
J6: Raspberry Pi Power/UART; Molex_Micro-Fit_3.0_43045-0612_2x03_P3.00mm_Vertical

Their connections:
+5V: J6.1, J6.2; also elsewhere on the board
GND: J6.3, J6.4; also elsewhere on the board
PI_RX: J6.5; also elsewhere on the board
PI_TX: J6.6; also elsewhere on the board

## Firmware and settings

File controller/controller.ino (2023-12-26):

#include <Arduino.h>
#include "src/updaters/robot_core.h"
#include "src/utils/time.h"

// TODO:
// Replace with the right pins - OK
// Add integration of activation pin, along with reset method

// Global variables

RobotCore* core;
RobotState state;
Clock clock;
Tick tick;

// Setting up the interrupts for encoders

void isr1() {
    core->motors[0]->encoder.hall_a_interrupt();
}

void isr2() {
    core->motors[1]->encoder.hall_a_interrupt();
}

void isr3() {
    core->motors[2]->encoder.hall_a_interrupt();
}

// Setting up the interrupt for current sense

volatile int icurrent_counter[NUM_MOTORS] = {0};    // Counter for current sense
volatile int maxSenseValue[NUM_MOTORS] = {0};       // Max sense value for current sense

ISR(TIMER5_COMPA_vect) {
    for (int i = 0; i < NUM_MOTORS; i++) {
        int senseValue = analogRead(state.motors[i].isense_pin);
        if (senseValue > maxSenseValue[i]) {
            maxSenseValue[i] = senseValue;
        }
        icurrent_counter[i]++;
        if (icurrent_counter[i] >= 5) {  
            core->motors[i]->state.icurrent = maxSenseValue[i];
            maxSenseValue[i] = 0;  
            icurrent_counter[i] = 0;       
        }
    }
}

// Setting up ADC clock

void setupADC() {
    // Set ADC prescaler to 16 for faster ADC readings.
    // increase prescaler for better accuracy (but slower).
    ADCSRA &= ~(bit(ADPS2) | bit(ADPS1));
    ADCSRA |= bit(ADPS2);
}

// Setting up timer interrupt


void setupTimerInterrupt() {
    noInterrupts(); // Disable interrupts

    TCCR5A = 0; // set entire TCCR5A register to 0
    TCCR5B = 0; // same for TCCR5B
    TCNT5  = 0; // initialize counter value to 0
    // set compare match register for 1hz increments
    OCR5A = 6531; // = (16*10^6) / (1*1024) - 1 (must be <65536)
    // turn on CTC mode
    TCCR5B |= (1 << WGM52);
    // Set CS52 and CS50 bits for 1024 prescaler
    TCCR5B |= (1 << CS52) | (1 << CS50);  
    // enable timer compare interrupt
    TIMSK5 |= (1 << OCIE5A);

    interrupts(); // Enable interrupts
}

void setup() {
    
    // Configure the robot state
    state.motors[0].lpwm_pin = 2;
    state.motors[0].rpwm_pin = 7;
    state.motors[0].hall_a_pin = 18;
    state.motors[0].hall_b_pin = 30;
    state.motors[0].gear_ratio = 1./82.;
    state.motors[0].ppr = 16;
    state.motors[0].isense_pin = 54;

    state.motors[1].lpwm_pin = 3;
    state.motors[1].rpwm_pin = 8;
    state.motors[1].hall_a_pin = 19;
    state.motors[1].hall_b_pin = 31;
    state.motors[1].gear_ratio = 1./82.;
    state.motors[1].ppr = 16;
    state.motors[1].isense_pin = 55;

    state.motors[2].lpwm_pin = 5;
    state.motors[2].rpwm_pin = 11;
    state.motors[2].hall_a_pin = 20;
    state.motors[2].hall_b_pin = 32;
    state.motors[2].gear_ratio = 1./82.;
    state.motors[2].ppr = 16;
    state.motors[2].isense_pin = 56;

    Serial.begin(BAUD_RATE);
    core = new RobotCore(state);

    // Attach interrupts
    attachInterrupt(digitalPinToInterrupt(state.motors[0].hall_a_pin), isr1, RISING);
    attachInterrupt(digitalPinToInterrupt(state.motors[1].hall_a_pin), isr2, RISING);
    attachInterrupt(digitalPinToInterrupt(state.motors[2].hall_a_pin), isr3, RISING);

    // Current Sense Setup
    setupADC();
    setupTimerInterrupt();

    // Set up onboard LED
    pinMode(13, OUTPUT);
}

void loop() {
    // Update the robot
    tick = clock.update();
    core->update(tick);
}

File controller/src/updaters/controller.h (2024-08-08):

#pragma once

#include "../utils/time.h"
#include "../utils/base_state_updater.h"

#include "../states/motor_state.h"

/**
 * This class is a custom adaptive PID controller that has been heavily
 * modified to work well for our system with the observation that PWM is 
 * roughly proportional to the measured speed of the motor.
 * 
 * We originally used the ArduPID library, but this was rewritten for better
 * readability, and to allow for more runtime configuration.
 * 
 * 
 * Compared to the ArduPID implementation, our code does the following differently:
 * 
 * 
 * *** Bias term is multiplied with the sign of the setpoint ***
 * 
 * I interpret this as adding the minimum PWM value to get the motor to start moving
 * 
 * 
 * *** The accumulated integral value is multiplied with the setpoint before being added to the output ***
 * 
 * Our motor has a fast response time and little inertia, intuitively it makes sense that at setpoint 0,
 * the integral term should be zero as well. 
 * 
 * Also makes use of the assumption that the motor speed is roughly proportional to the PWM value.
 * Effectively, this means that the controller converges on creating a coefficient that forms a linear
 * relationship between the setpoint and the measured value.
 * 
 * Under this new scheme, the I term becomes the main contributor to the output. The controller would be able 
 * to work even without the P and D terms (purely adaptive feedforward control), but with the addition of the two 
 * terms, the controller is able to converge faster and with less overshoot. Moreover, the controller is able to
 * adapt to changes in the system, such as a change in the load on the motor.
 * 
 * However, note that with this modification, the I term contributes a lot more especially when the setpoint is high.
 * A smaller value should be chosen for stability. The P term should be tuned similarly to a normal PID controller.
 *
 * In regular PID systems, the I term accumulator is usually initialized to 0. However in our system this represents
 * the linear relationship between the setpoint and the measured value. Therefore, if it is initialized to 0, the
 * controller takes a long time to slowly converge on the correct value. To speed up the process, the accumulator
 * should be initialized to a value that is close to the correct value. Perhaps having persistent storage of the
 * accumulator value would be useful. It could be implemented by storing the value in EEPROM, and also would be useful
 * for ROS to be able to change the accumulator value.
*/

#define OPEN_LOOP 0 // No feedback control
#define CLASSIC_PID 1 // Original ArduPID implementation
#define CLASSIC_PID_B_I_FLIPPING 2 // Bias and integral term flips polarity when setpoint changes sign
#define ADAPTIVE_PID 3 // I is multiplied with setpoint before being added to output

/**
 * A custom adaptive PID controller that updates motor output based on the measured speed of the motor
 */
class Controller : public BaseStateUpdater<MotorState> {
    private:
        double last_error = 0;
        short last_setpoint_polarity = 0;
    public:
        Controller(MotorState& state) : BaseStateUpdater<MotorState>(state) {}
        void update(Tick& tick) {
            if (state.control_mode == OPEN_LOOP) {
                state.output = state.setpoint;
                state.error = 0;
                last_error = 0;
                last_setpoint_polarity = 0;
                return;
            }
            if (state.encoder_dt >= 0) { // Only update if there is a fresh encoder reading. Otherwise, the readings mean nothing!
                state.error = state.acceleration_bounded_setpoint - state.velocity; // Calculate error
                if (state.error >= state.deadband_min && state.error <= state.deadband_max) {
                    state.error = 0;
                }
                double p_out = state.p_in * state.error; // Calculate proportional term
                double d_out = -state.d_in * state.acceleration; // Calculate derivative term
                // Calculate integral term
                // Polarity: -1 if setpoint is negative, 1 if setpoint is positive, 0 if setpoint is 0
                double setpoint_polarity;
                if (state.control_mode == CLASSIC_PID) {
                    setpoint_polarity = 1;
                    last_setpoint_polarity = 1;
                } else { // CLASSIC_PID_B_I_FLIPPING or ADAPTIVE_PID
                    setpoint_polarity = (state.acceleration_bounded_setpoint == 0) ? 0 : (state.acceleration_bounded_setpoint >= 0) ? 1 : -1;
                }

                double bias_out = state.bias * setpoint_polarity; // Calculate bias term

                double i_temp = state.i_accumulator + (state.i_in * state.encoder_dt * 
                    (state.error * setpoint_polarity + last_error * last_setpoint_polarity) / 2 // Trapezoidal integration
                );

                // Constrain using windup limits
                i_temp = constrain( i_temp, state.i_accumulator_min, state.i_accumulator_max ); // Temporary variable before we constrain with limits

                // Constrain using output limits, so the integral term doesnt grow if we saturate the output
                double pdb_out_temp = p_out + d_out + bias_out; // Calculate output without integral term
                if ( state.control_mode == CLASSIC_PID || state.control_mode == CLASSIC_PID_B_I_FLIPPING ) {
                    double i_out_max = constrain(state.output_max - pdb_out_temp, 0, state.output_max); // We constrain the integral term to the range of the output just to be safe
                    double i_out_min = constrain(state.output_min - pdb_out_temp, state.output_min, 0); 
                    i_temp = constrain( i_temp, i_out_min, i_out_max );
                } else if ( state.control_mode == ADAPTIVE_PID && state.acceleration_bounded_setpoint != 0 ) {
                    // double i_out_max = constrain((state.output_max - pdb_out_temp) / state.setpoint, 0, state.output_max); // We constrain the integral term to the range of the output just to be safe
                    // double i_out_min = constrain((state.output_min - pdb_out_temp) / state.setpoint, state.output_min, 0);
                    // i_temp = constrain( i_temp, i_out_min, i_out_max );
                }
                state.i_accumulator = i_temp;

                // Calculate output
                double temp_out;
                if ( state.control_mode == CLASSIC_PID || state.control_mode == CLASSIC_PID_B_I_FLIPPING ) {
                    temp_out = p_out + d_out + state.i_accumulator * setpoint_polarity + bias_out;
                } else if ( state.control_mode == ADAPTIVE_PID ) {
                    temp_out = p_out + d_out + state.i_accumulator * state.acceleration_bounded_setpoint + bias_out;
                }
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

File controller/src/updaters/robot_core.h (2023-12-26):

#pragma once

#include "../utils/time.h"
#include "../utils/base_state_updater.h"

#include "../states/motor_state.h"
#include "../states/robot_state.h"

#include "motor.h"
#include "communication.h"
#include "power_manager.h"

#include "../defs.h"

class RobotCore : public BaseStateUpdater<RobotState> {

    public:

        Communication* communication;
        Motor* motors[NUM_MOTORS];
        PowerManager power_manager;
        int motor_reset_pin = 36;
        double motor_reset_duration = 0.05; // Minimum time to keep the motor reset pin LOW (in seconds)
        double motor_reset_time_elapsed = 0; // Time elapsed since the motor reset pin was set LOW (in seconds)
        bool motor_reset_pin_state;
        
        RobotCore(RobotState& state) : BaseStateUpdater<RobotState>(state), power_manager(state) {
            
            // Let's initialize the communication
            communication = new Communication(state);

            // Then initialize all the motors
            for (int i = 0; i < NUM_MOTORS; i++) {
                motors[i] = new Motor(state.motors[i]);
            }

            // Set HIGH for motor reset pin
            motor_reset_pin_state = true; // Initialize as HIGH
            pinMode(motor_reset_pin, OUTPUT);
            digitalWrite(motor_reset_pin, HIGH);

        }

        ~RobotCore() {

            // Delete the communication
            delete communication;

            // Delete all the motors
            for (int i = 0; i < NUM_MOTORS; i++) {
                delete motors[i];
            }

        }

        void handleMotorReset(Tick& tick) {

            if (state.motor_reset_flag && motor_reset_pin_state) { // If need to reset motors and currently HIGH (not resetting, and requesting reset)
                digitalWrite(motor_reset_pin, LOW); // We set the motor driver reset pin to LOW
                motor_reset_pin_state = false; // Update the state
                motor_reset_time_elapsed = 0; // Reset the time elapsed
                state.motor_reset_flag = false; // Reset the flag
            } else if (motor_reset_time_elapsed >= motor_reset_duration && !motor_reset_pin_state) { // If the reset duration has elapsed and currently LOW (resetting)
                digitalWrite(motor_reset_pin, HIGH);
                motor_reset_pin_state = true; // Update the state
            } else if (!motor_reset_pin_state) { // If currently LOW (resetting)
                motor_reset_time_elapsed += tick.dt; // Add time elapsed
            }
            // Remaining case: Not resetting, and not requesting reset, do nothing
            
        }

        void update(Tick& tick) {

            // Let's first update all the motors
            for (int i = 0; i < NUM_MOTORS; i++) {
                motors[i]->update(tick);
            }

            // Then update the power manager
            power_manager.update(tick);

            // Then update the communication
            communication->update(tick);

            // Then handle the motor reset
            handleMotorReset(tick);

        }

};

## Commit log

2023-05-30 fixed some include issues and library install
    [controller.ino]
2023-05-31 added pid parameter controls
2023-05-31 removed potentially problematic consts
    [controller.ino]
2023-05-31 control node functional but unstable
    [controller.ino, pid_motor.cpp, ros_serial_client.cpp]
2023-06-01 functional PID motor control!
2023-06-02 non-functional ros_control controller
    [controller.yaml]
2023-06-06 added odometry calculation
2023-06-06 added odometry publishing
2023-06-10 started new implementation of kinematics
2023-06-10 inverse kinematics, and composition
2023-06-10 added odometry to new .h file
2023-06-10 fixed kinematics
2023-06-10 fixed odometry numerical stability issue
2023-06-10 changed to dumber encoder
2023-06-10 migrated files in
    [colours.xacro, frame_ultra_low_poly.stl, inertial_macros.xacro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]
2023-06-12 fixed wheel direction and names
2023-06-13 added model view
    [controller.yaml, gazebo_wheel_pid.yaml, robot.urdf.xacro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]
2023-06-13 changed to using joint state controller
    [controller.yaml, robot.urdf.xacro, robot_core.xacro]
2023-06-13 broken gazebo
    [robot_core.xacro]
2023-06-13 initial commit for rbc circuits
    [brain.kicad_sch, motor_controller.kicad_sch, power_module.kicad_sch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]
2023-06-14 added 5V reg circuit
    [power_module.kicad_sch, rbc_circuits.kicad_sch]
2023-06-15 motor shield circuit
    BTN7030-1EPA
    [brain.kicad_sch, motor_controller.kicad_sch, motor_shields.kicad_sch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]
2023-06-15 added joint state controller
2023-06-15 added laser
    [robot_core.xacro]
2023-06-15 slam stuff
    [robot_core.xacro]
2023-06-16 updated shield schematic
    [motor_shields.kicad_sch]
2023-06-18 diagram and cleanup
    [colours.xacro, frame_ultra_low_poly.stl, inertial_macros.xacro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]
2023-06-22 improved PID algorithm
    added mirrored bias to PID
    modified integer term to switch polarity depending on setpoint polarity
    disabled stalling prevention
    [controller.ino, encoder_naive.h, pid_motor.cpp]
2023-06-22 changed stall prevention
2023-06-22 added quantization error as deadband
    [encoder_naive.h, pid_motor.cpp]
2023-06-22 fixed bugs with quantization error calc
    [encoder_naive.h, pid_motor.cpp]
2023-06-23 started work on PID rewrite
2023-06-24 general flow set up
2023-06-24 encoder implementation
2023-06-25 pid implemented?
2023-06-25 fixed pid
2023-06-25 motor done
2023-07-10 proposed split
    [colours.xacro, controller.yaml, frame_ultra_low_poly.stl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]
2023-07-25 controller pcb rev 1
    [motor_controller.kicad_sch, motor_shields.kicad_sch, power_module.kicad_sch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]
2023-08-13 omniwheel base custom controller; changed PWM freq to accommodate new ICs
2023-08-13 LED movement signal; ssh uncomment
2023-08-14 Arduino GPIO UART update
2023-08-20 added current sense pins
2023-08-22 added timerinterrupt for current sense
2023-08-22 current sense now process all 4 motors
2023-08-22 onboard led fixed
2023-08-22 outline of lidar launch
2023-08-23 current sense up and running
2023-08-23 update lidar position
    [robot_core.xacro]
2023-08-25 fixed wheel configuration
2023-09-06 fixed odometry
    [robot_core.xacro]
2023-09-09 PCB Rev2.0 publish
    It's here
    [MCU.kicad_sch, motor_controller.kicad_sch, motor_shields.kicad_sch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]
2023-09-11 initial commit
    This branch changes odom to a 3 wheel configuration
2023-09-11 updated wheel coordinates&angles
2023-09-13 removed .old
    [colours.xacro, controller.yaml, frame_ultra_low_poly.stl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]
2023-09-13 updated wheel position
    wheel-origin distance: 0.45m -> 0.2m
2023-09-13 updated mesh for chassis 2.0
    [frame_ultra_low_poly.stl]
2023-09-13 updated wheel 1 coordinates
    [robot_core.xacro]
2023-09-13 updated wheels xacro
    [frame_ultra_low_poly.stl, robot_core.xacro]
2023-09-13 enabled slam
    [robot_core.xacro]
2023-09-15 mesh successfully loaded
    [robot_core.xacro]
2023-09-15 updated lidar location and orientation
    [robot_core.xacro]
2023-09-15 removed redundant mesh
    [frame_ultra_low_poly.stl]
2023-09-15 updated chassis inertial and collision model
    [robot_core.xacro]
2023-12-24 trying new board
2023-12-26 initial commit
    included battery level detection library
2023-12-26 power management logic and reset pin
2023-12-26 modify for 3 motors
2023-12-28 changed messages to 3 wheels
    [robot_core.xacro]

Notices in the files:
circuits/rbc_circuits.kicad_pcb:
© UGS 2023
